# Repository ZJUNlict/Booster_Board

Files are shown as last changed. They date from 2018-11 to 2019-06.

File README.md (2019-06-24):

# ZJUNlict Booster Board Description

RoboCup 2019 Competition Version

Modifications are made to the design of the [booster board 2018 RoboCup Version](https://github.com/ZJUNlict/Booster_Board/releases). 

The major modifications are:

* Use Molex Connectors for capacitors and coils for easier assembly and maintenance.
* Add three MP1584EN (12V, 5V, 3.3V) modules for DC-DC conversion.
* Change the MOSFETs to IPB64N25S3-20 or IPB200N25N3GATMA1 with D2PAK package.

The photos of booster board 2019 version are shown below. 

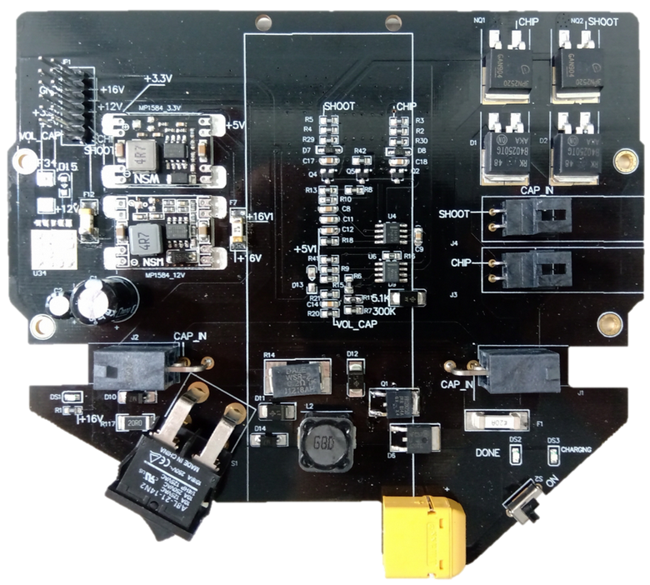
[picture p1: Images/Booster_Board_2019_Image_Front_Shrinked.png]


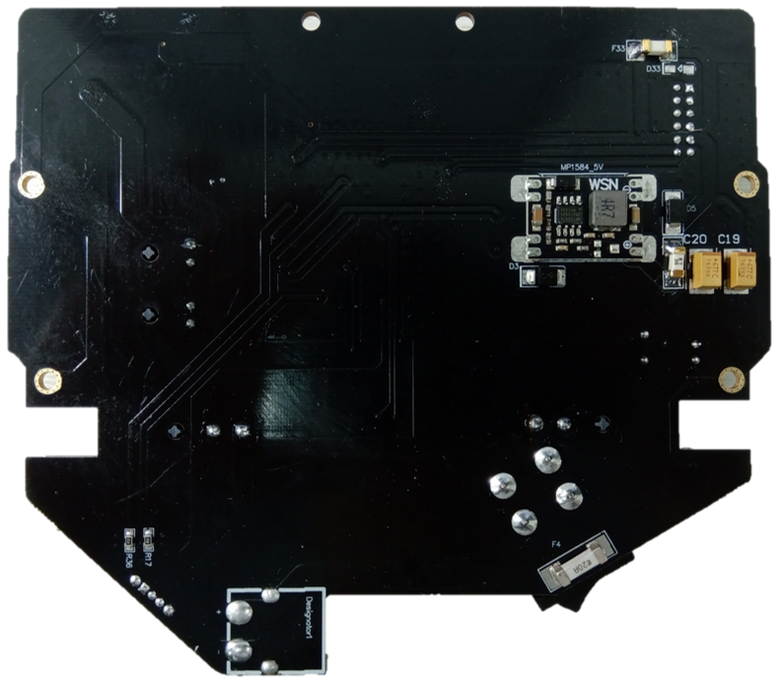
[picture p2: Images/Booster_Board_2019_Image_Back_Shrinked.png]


--------------------------

RoboCup 2018 Competition Version

The booster board is used to charge capacitors and discharge via shoot and chip coils. The 2D and 3D design views are shown below. (The board is designed using [Altium Designer](https://www.altium.com/altium-designer/) 17.1)

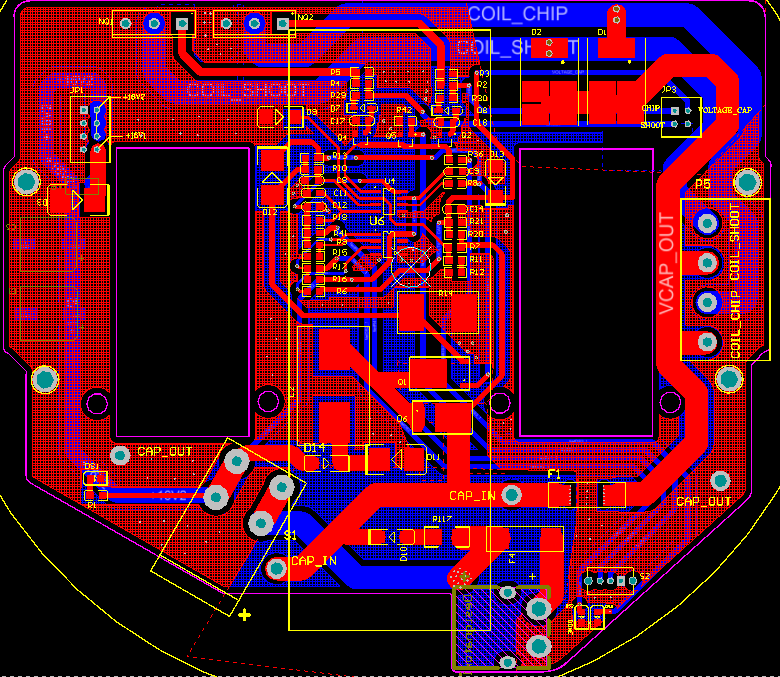
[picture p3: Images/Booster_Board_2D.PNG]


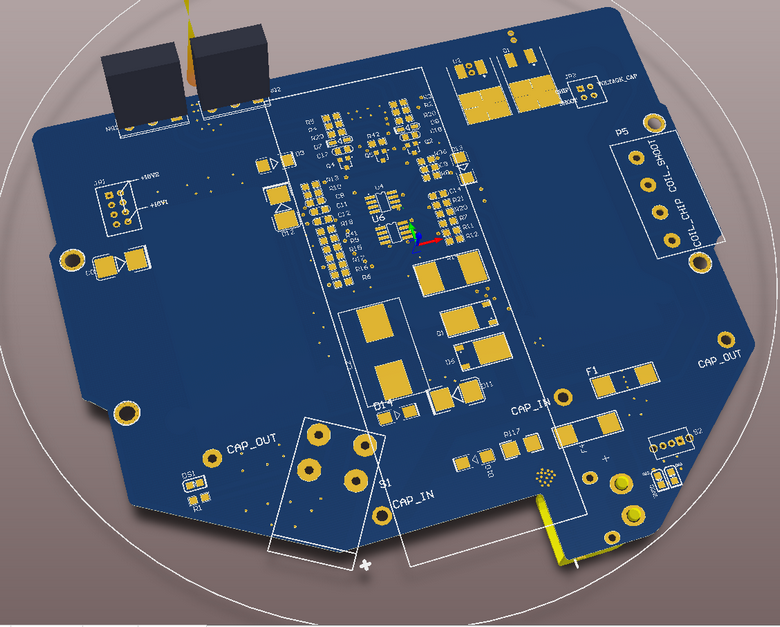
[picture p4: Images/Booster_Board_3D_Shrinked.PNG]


The main features are:

* Current-mode PWM controller UC3843 acts as a booster converter to charge two capacitors (each with 2200 uF capacitance and voltage rating at 250V) to 225V (Adjustable by simply modifying the voltage feedback resistor pair).
* Two MOSFETs (IPP200N25N) control the discharge duration of the cpacitors.
* A voltage comparator is used to show if the capacitors are charged through an LED to avoid accidental electric shock.
* Limiting voltage and current to the main borad.

The photos of the booster board are shown below as references. 

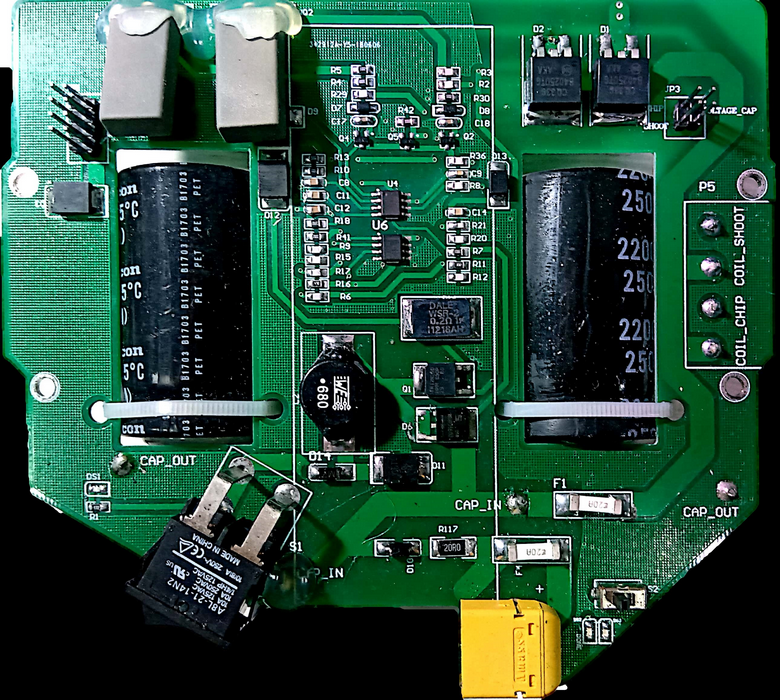
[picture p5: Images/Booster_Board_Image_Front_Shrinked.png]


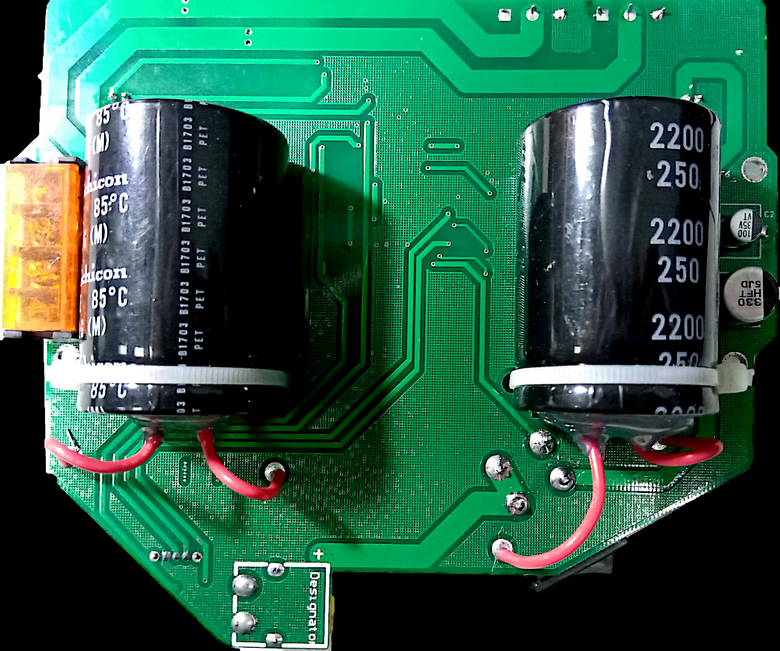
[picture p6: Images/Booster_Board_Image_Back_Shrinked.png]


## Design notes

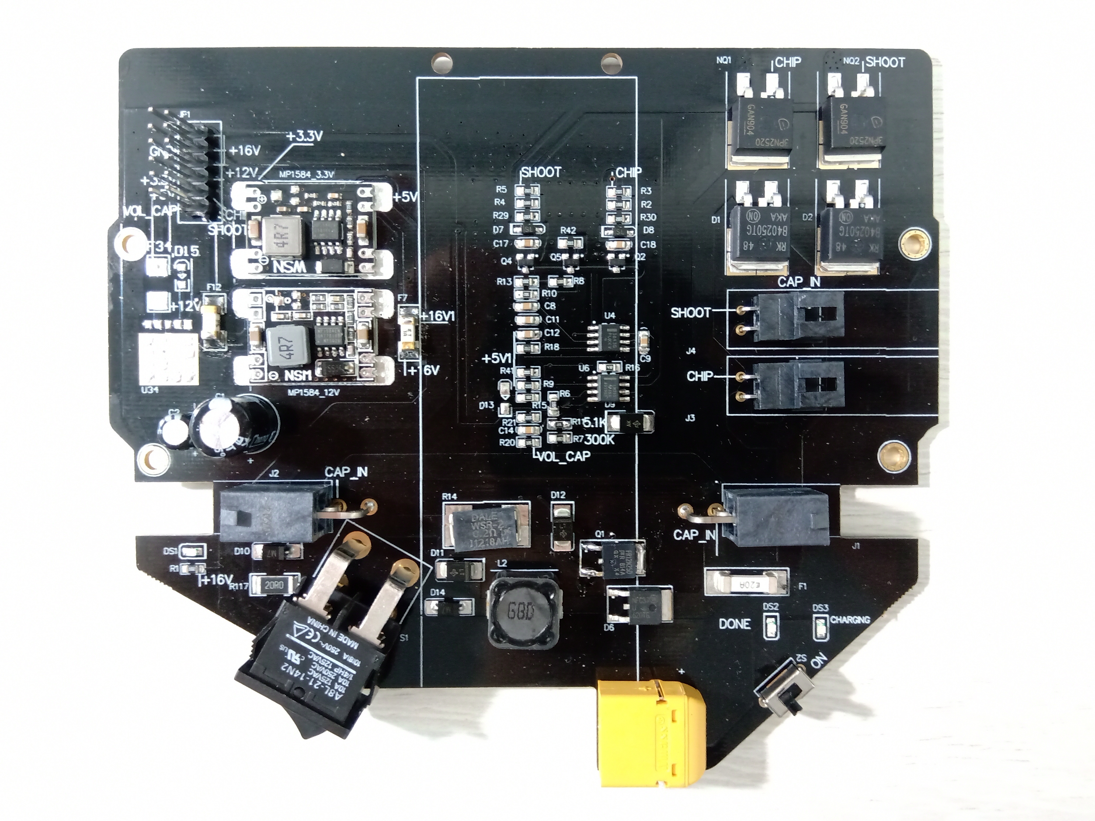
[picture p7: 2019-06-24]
Images/Booster_Board_2019_Image_Front.jpg

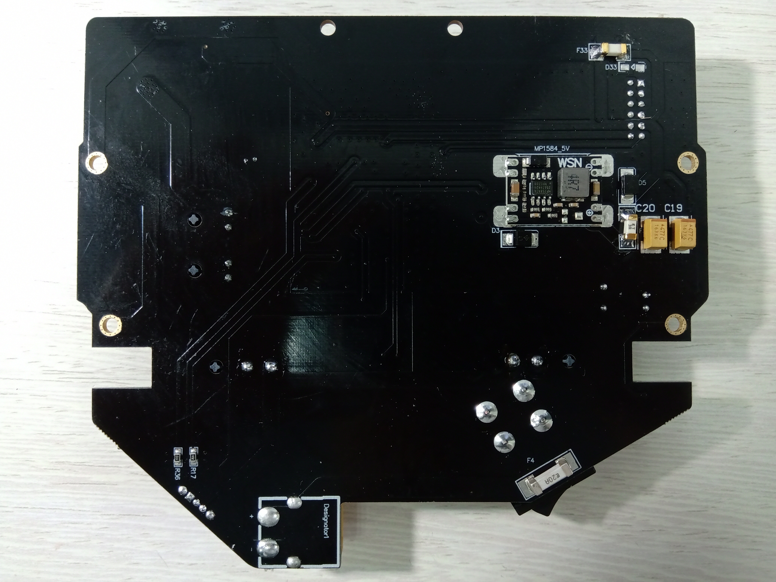
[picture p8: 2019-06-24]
Images/Booster_Board_2019_Image_Back.jpg

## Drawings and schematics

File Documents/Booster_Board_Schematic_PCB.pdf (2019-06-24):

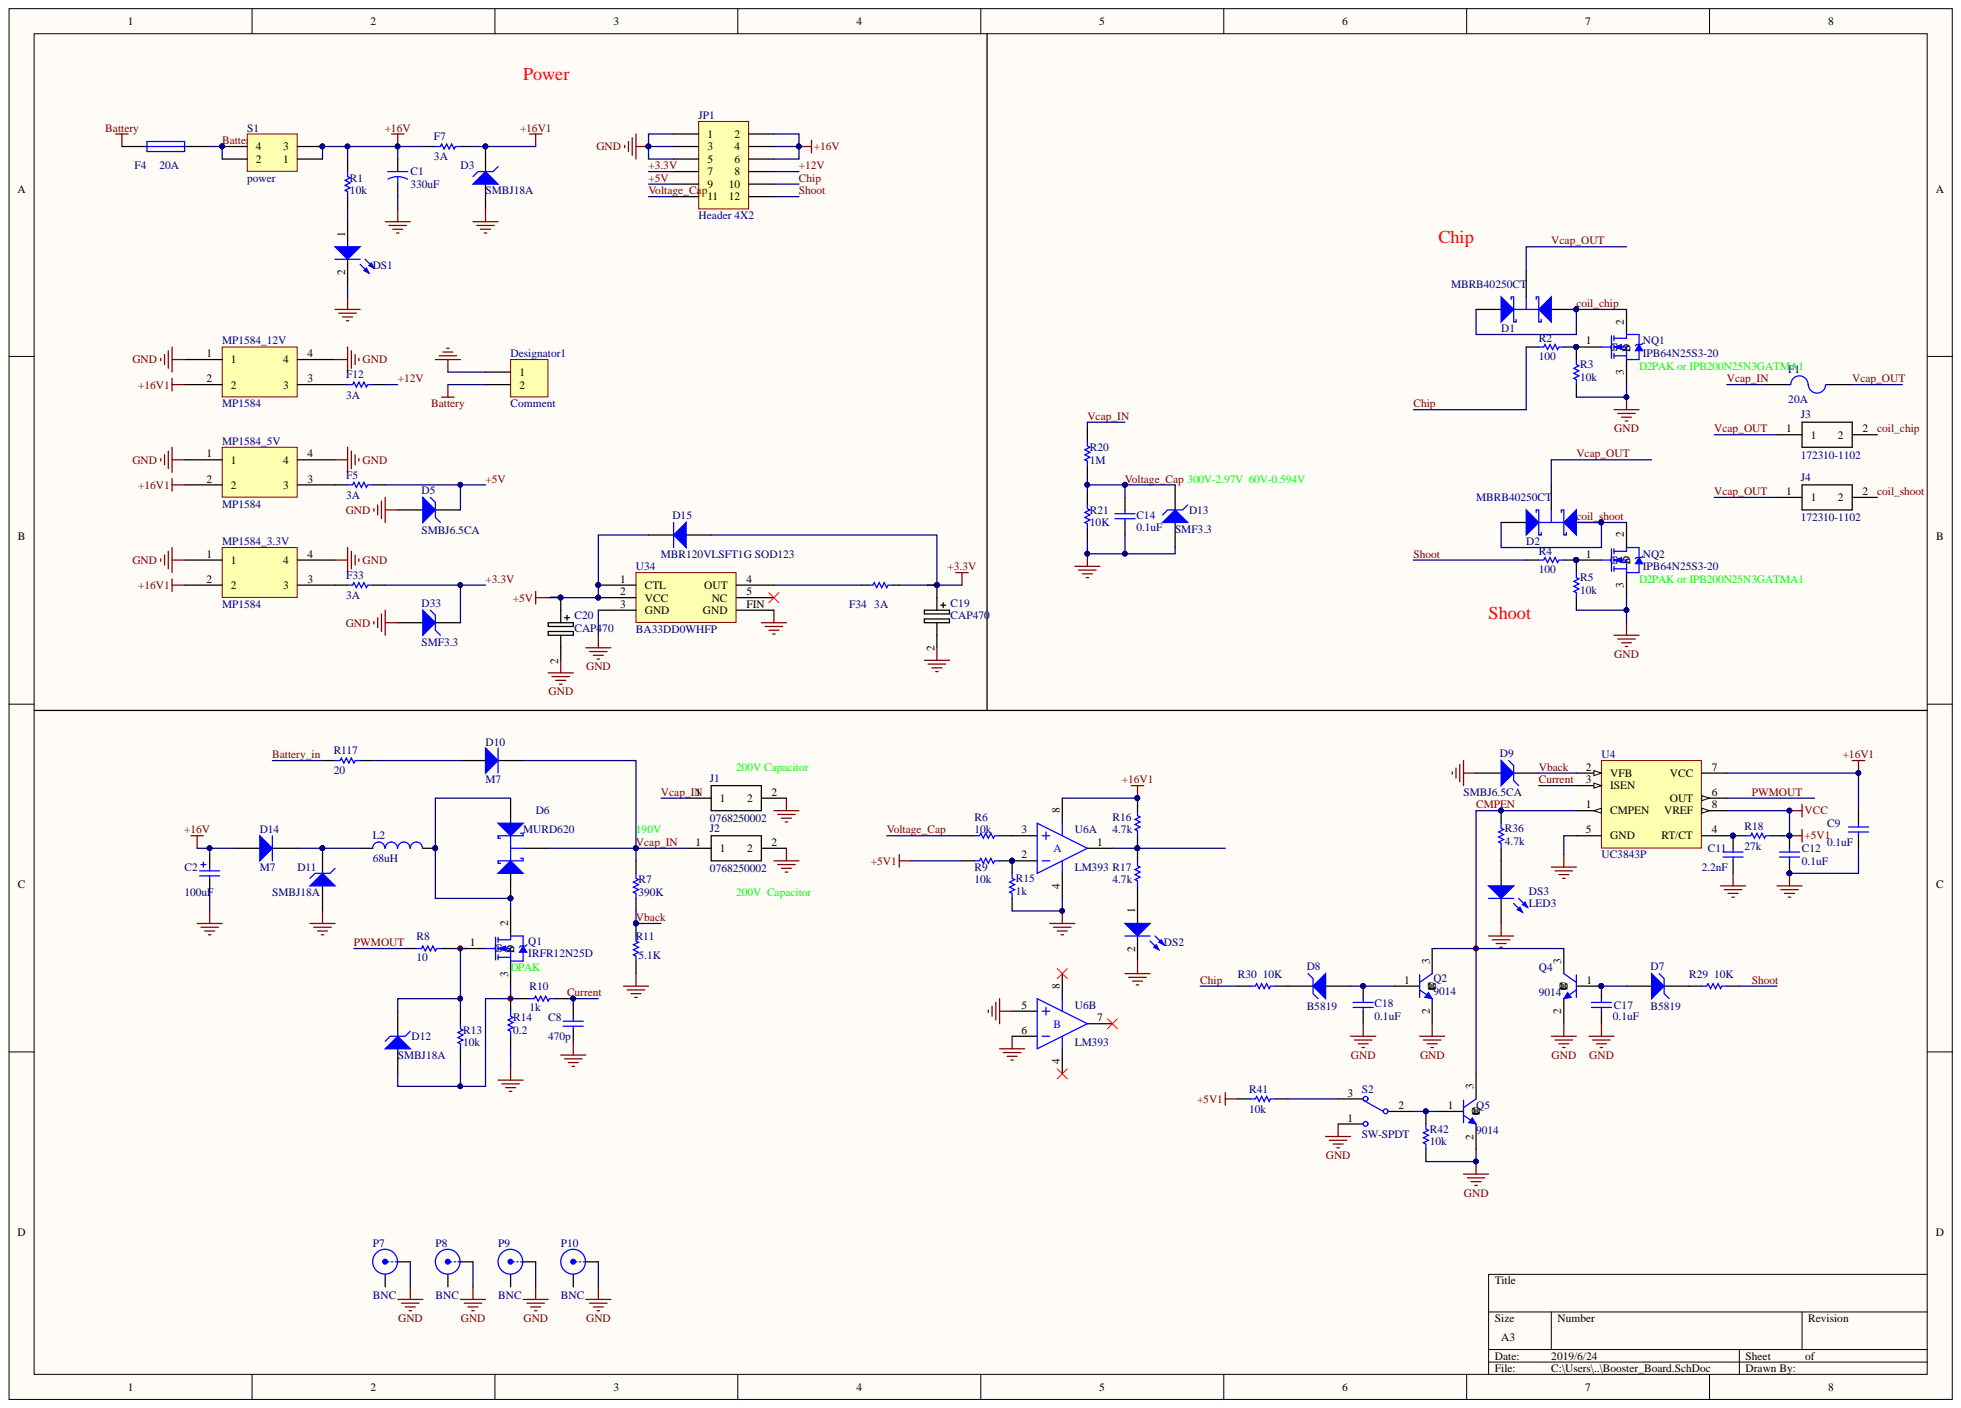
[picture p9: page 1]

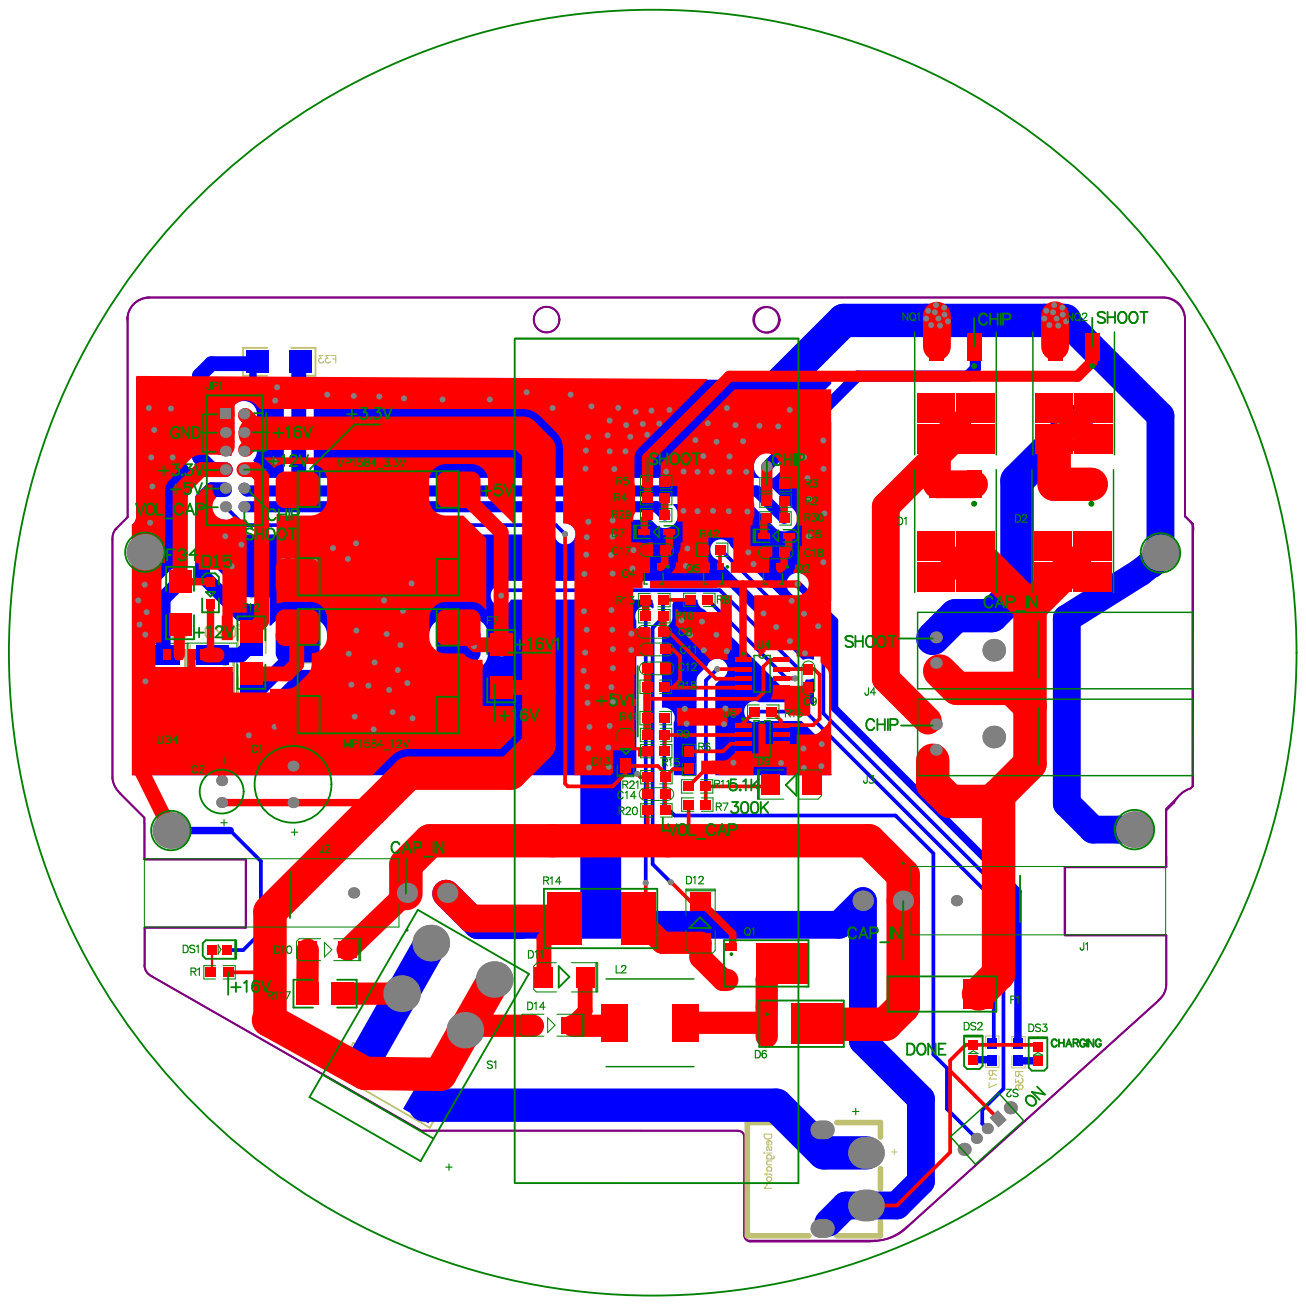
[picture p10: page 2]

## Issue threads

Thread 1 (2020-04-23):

Enquiry on the method in amplifying the voltage in 'Booster_Board'

Turner-sim, 2020-04-23:
I trully appreciate on what you guys are sharing this awesome works here.
Currently I am working on some project that need the implementation of this booster board, which I am trying to study on your contribution here, but I wonder about some issue about your circuit.
For charging a 200V capacitor, it seems to have amplify certain element somewhere( to increase almost 190V)
but I could not find that how make it.
If you mind.. please give me a clue for several issues.
1. How much voltage came on 'Battery_in' node
2. How did you make amplifing that voltage
3. in communication protocol, it contain 7bits for shoot(or chip) impact control.
Then, on your circuit, how did you implement on your circuit for it works.
Take care,
Shim

icly, 2020-04-23:
Thank you for using our design as a reference. I'll explain the issues you have in the following.
1. The voltage at the ‘Battery_in' node is the direct input from a 4S1P LiPo Battery which is about 15V to 16.8V. The voltage can be changed as long as the UC3843 ic can work properly for the charging circuit.
2. The principle used is called boost converter. https://en.wikipedia.org/wiki/Boost_converter
3. In the communication protocol, the 7bits represent the shoot/chip power. It is controlled by the discharge time using the MOSFET. In the mainboard, the MCU will generate high-level signals with different pulse widths to a pre-driver and then drive the MOSFET to discharge.
If you have further questions, just post it here.
Best regards,
Lingyun

Closed 2020-08-18.

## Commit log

2018-11-11 Upload Booster Board PCB files
    [Booster_Board.PcbDoc, Booster_Board.PrjPcb, Booster_Board.SCHLIB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]
2018-11-15 Add board description
2019-06-24 Add RoboCup 2019 Version
    [Booster_Board.PcbDoc, Booster_Board.PcbLib, Booster_Board.PrjPcb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]
